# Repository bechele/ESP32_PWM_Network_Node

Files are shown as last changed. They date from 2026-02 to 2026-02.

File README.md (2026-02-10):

## Network device to drive Servos for Animatronics:

With the latest Software 3.0 the Bechele software (https://github.com/bechele/bechele) now supports beside the existing PCA9685 PWM Boards also network devices, based on cheap ESP32 modules. Each network device may handle 16 Servos or 16 Relais or a desired mixture of both. All the data transfers from the Host (Raspi) is realized using broadcast transmissions, where all devices (nodes) receive the same data packets. According to the node configuration, the node takes the data from the packet that is intended for it. This way there is plenty of time to drive 700 Servos @ 44 ESP32 nodes, or 11000 relais @ 700 nodes with a 50ms refresh rate. Network devices may be connected via Ethernet or WiFi. Of course Ethernet driven nodes are more stable than via Wifi. The board exists in two flavours. A smaller SMD version and a larger version unsing conventional parts. For both versions you may download the gerber files and also the kicad source, so you can order a PCB from your desired PCB manufacturer. The smd version is for skilled people who know how to handle and solder SMD parts. The conventional Version uses mainly larger parts that are much easier to solder onto the PCB. Which one you use is up to you. The function is identical.<br><br>
**Note: Using Wifi is by far not as safe as using ethernet. To use WiFi, you need to make sure, the WiFi router is very close to the network devices, since the RSSI (Received Signal Strength Indicator) must be below 70 dB, (you may read the RSSI value during boot, when connecting a serial monitor to the TX pin of the device). Otherwise you will notice lots of missing packets – means the movement of your servos will be not continuous. Also you need an environment where there are only few other Wifi radio sources. If there is a lot of other traffic around, you will encounter the same problems. This is due to the working principle of WiFi and has nothing to do with the software. Wifi is not intended for real time control of devices ! So my recommendation is to use W5500 Ethernet modules. In a test using Ethernet with 700 configured Servos @ 50 ms refresh rate (means every 50 ms all servos got new data), none of the packets went lost over a longer time, so ethernet is quite safe.**
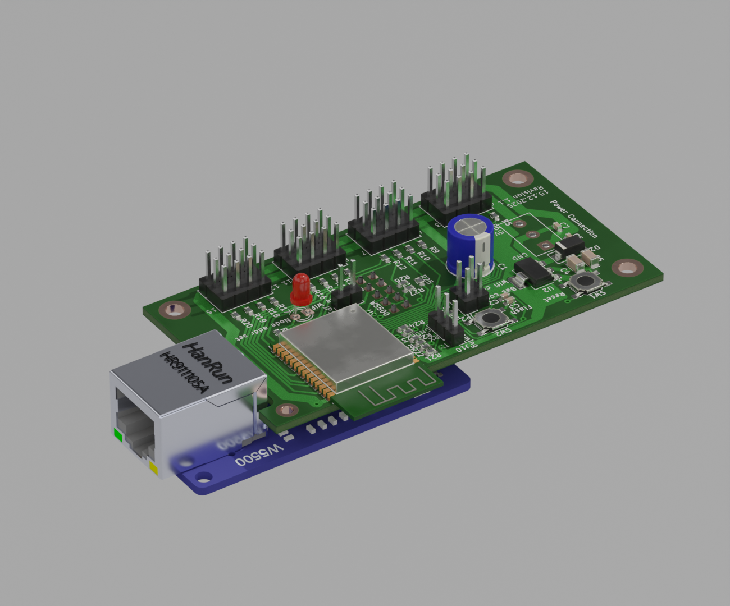
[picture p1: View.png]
ESP32 Node Image


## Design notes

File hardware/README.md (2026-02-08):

## The ESP32_PWM_NODE_PCB exists in two flavours:
- A SMD based version for skilled people, able to solder tiny SMD parts, or for automatic assembled PCBs.
- A PCB based on conventional parts for easier assembly.

Note: Both PCBs have an identical function and run with the same firmware.

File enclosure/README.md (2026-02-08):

## Enclosures - cases for the ESP32_PWM_NODE_PCBs
There exist four different cases for ESP32_PWM_NODE PCBs - depending on which PCB you use and if you want to use the W5500 Ethernet network module:
- An enclosure for the SMD based PCB with W5500 Ethernet module.
- An enclosure for the SMD based PCB, but omitting the W5500 Ethernet module.
- An enclosure for the conventional parts based PCB with W5500 Ethernet module.
- An enclosure for the conventional based PCB, but omitting the W5500 Ethernet module.

All enclosures are available as .stl file for 3d printing and as an .obj file for reworking.

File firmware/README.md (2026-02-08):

## This firmware is intended for the ESP32_PWM_NODE_PCB.
It manages to receive broadcast data packets from the bechele software https://github.com/bechele/bechele and controls servos and relais connected to the ESP32_PWM_NODE_PCB.
The firmware needs the enclosed Library that derives from:
https://github.com/ramadhanafif/Ethernet2-W5500-ESP32.
For details read the documentation in folder Documentation and/or visit my web site: http://bechele.de

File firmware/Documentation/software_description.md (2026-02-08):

# Software description for the Bechele Project network devices.
## Features of the Bechele Network devices:
* The bechele project can use new, extremely cheap hardware, based on a ESP32 Wroom 32 or ESP32E Wroom. Furhter called nodes.
* very large installations may be easily realized using the bechele software, since Hundrets of nodes may be controlled simultaneously by the bechele software.
* A node has 16 output channels - means 16 Servos may be connected directly to one small hardware box.
* A node may also be used to connect binary outputs, such as relais boards
* The 16 output pins can be split into partially Servo or relais outputs in a flexible way.
* Currently approx. 32000 nodes may be addressed in one network.
* A node may have a W5500 device attached, so it gets its data via 100BaseT Ethernet.
* All nodes have built in Wifi.
* The device can be fully configured over the network, once the basic configuration has been done. 
* The network traffic remains on an absolute minimum, since data is sent via broadcast to all nodes at once. 
* With the limited packet length of 1432 bytes per network frame, approx 700 nodes may be controlled by the bechele software simultaneously. If more is required, the software may be adapted easily.
The default 50 ms (20Hz) refresh time allows seamless servo movements without stucks or visible delays.

## Description of the internal software function
The Bechele project uses an ESP32 Wroom 32 or ESP32E Wroom as an output device in the Ethernet and WLAN network. The ESP can receive data transmitted via broadcast from the network on port 7625. The user datagram for normal operation has an indefinite length but always begins with a data word (16 bits) containing the number of transmitted user data words. The second data word contains a sequential counter, which is not initially important for the receiver. This is followed by further data words (16 bits) which, for servo data, are in the range of 0-4095 (0FFFh) and are output as PWM values to the ESP's available PWM outputs (max. 16), depending on the configuration. For relay data, the valid value range is between 0 and 65535. A single data word can control all 16 outputs of the ESP. The outputs provide sufficient drive current to control model servos or relay modules. Depending on the software configuration, each of the 16 outputs can be operated either as a servo output with PWM or as a digital output with a constant level. Mixed operation between servo and relay outputs is also possible. The specific word in the datagram used for output is defined in configuration registers. This can be any data word in the datagram; it does not need to be synchronized to the 16 available outputs (steps), but it must be synchronized to the data word boundary. This means that the start word is specified in the configuration register in word steps, not as a byte position in the datagram. There can be multiple of these modules in the network, referred to as nodes. The maximum number of nodes in the network is set to 32765. As a result, the most significant bit in the length field of the datagram is not used for output addressing. If the length word (the first word in the datagram) contains a value greater than 32767, then the payload in the datagram is interpreted as a configuration instruction. Each node has a jumper input port (Bas conf) that is set to enable a basic configuration for the node. Nodes without the jumper set will not respond to the length value of 32768, as they are not in basic configuration mode. In basic configuration mode (with the jumper set) the sender of the broadcast will send the Ethernet address in the first six payload data words, followed by the node address and a 16-bit checksum. The ESP remembers its addresses, provided the checksum is correct, and stores them in NV memory (as an address register). The basic configuration datagram has a length of seven payload data words plus the checksum, resulting in a total length of 20 bytes. Once the ESP has received its Ethernet and node addresses, it automatically reboots when the jumper is removed. After the reboot, the new MAC and node addresses are applied. If a valid address exists in NV memory, a permanently assigned output port is set to 1. An LED connected to the node signals to the user that the address and MAC address for that node have been set. The address range for node addresses extends from 32769 (node 1) to the word boundary of 65533 (node 32765). If the first datagram word contains the node's address (+32768), the datagram's payload is considered the configuration for that node. Incoming configuration data is stored in 16-bit configuration data registers located in the NV data area or in the ESP's RAM. Multiple registers can be addressed simultaneously in a configuration datagram. Starting with data word 2 (word 0 encodes the node address, and word 1 is the sequential counter), each subsequent word is considered the register address, and the following word is the register content. The number of registers in a configuration datagram is undefined. As long as the datagram does not end, any two consecutive data words are treated as a single register instruction. Both configuration data and user data are broadcast to port 7625. For later physical node identification in a configured network, the configuration program nodeconfig.pl can send a blink command (register 128) to the node address to be identified, whereupon the node's LED blinks at a rate of 0.5 seconds. All configuration commands and PWM user data use a 16-bit checksum.

## The following registers in the NV memory are occupied:
```
Registers 0-5: Ethernet address of the node. 
6: Node address. 
7: Number of PWM outputs. 
8: Start word in the payload datagram (equal to the servo number in the operating program) containing the payload data applicable to this node. 
9: Pin number to which the PWM start word is output. All subsequent PWM data words are output to the following pins until the number (7:) is reached. 
10: Number of output pins reserved for relays. 
11: Data word in the payload datagram (servo number) containing the bit data for the output pins, where 16 bits represent 16 outputs. 
12: Pin number to which the first bit in the payload data word is mapped.
```
## The following registers in RAM are active: 
```
Register 128: Blinking active
Register 129: Blinking duration in seconds - currently unused by the configuration software. 
Register 130: Node reset - as soon as this register is set to 1, the ESP performs a reboot. 
Register 131: Status report to host via UDP (unicast) on port 7626. 
Register 132: Unconfig Node - if this register is set to 1, all registers are set to the default value 0 and a reboot is performed. This means the box will then be in its factory default state and must undergo a basic and node configuration before use.
```
## Two additional commands exist that are executed by all nodes on the network.

1. 65535 in the datagram's length word: Deactivates all PWM outputs. This is usually issued after a session ends to protect the servos.
2. 65534 in the datagram's length word: Restarts all nodes.

# Hardware:
A W5500 network adapter may be connected. If it is detected, it is initialized and Wi-Fi is disabled. If initialization fails, the node will still wait for a network connection via Ethernet - meaning there is no fallback to Wi-Fi.
If the node should use Wi-Fi, the "force Wi-Fi" jumper can be removed - this step requires a reboot.
The ESP obtains its IP network address via DHCP. In Ethernet mode, the ESP does not respond to unicast packets. The only communication with the ESP occurs via broadcasts on port 7625. Therefore, a network ping provides no information about the node's functionality.
The initial Ethernet address is set to DE:AD:BE:EF:00:01 in basic configuration mode (Bas Conf Jumper). This means that each module must be initialized separately, one after the other; otherwise, the same Ethernet address will be assigned to two or more nodes during basic configuration.

# Configuration procedure for Ethernet and Wi-Fi (after basic Wi-Fi configuration):
```
1. Set the Basic Config jumper.
2. Reset the node using the reset button on the board.
3. Set the node address in the configuration program nodeconfig.pl - the Ethernet address will be assigned automatically.
4. Press the Basic Config button in the configuration program.
5. Remove the Basic Config jumper from the node. This will automatically reboot the node. After a few seconds, the LED on the node should light up. This indicates that the basic configuration was successful.
6. Select the node address that was just set - if it is not already active - and use the "Get_Node_Status" button to display the node's configuration. If OK, you can proceed to step 7.
7. Set the remaining configuration parameters, which are usually different for each node.
8. Press the "Send_Node_Setup" button - the remaining parameters will be set. If the associated automatic check is successful, the configuration for this node is marked as "confirmed" in the database used by nodeconfig.pl.
9. The node is then ready to receive and output PWM and binary data. No further configuration is required after switching the node off and on again.
```
## Configuration procedure for Wi-Fi:
```
Note: The jumper "0= force wifi" must not be set:
1. Activate the Wi-Fi manager via the "Wifi Conf" jumper.
2. Reset the node using the reset button on the board.
3. Select the access point "ESP32_PWM_Node" on the host (smartphone or computer).
4. The Wi-Fi manager will start automatically, depending on the device.
5. Configure the Wi-Fi network (SSID and Wi-Fi password).
6. Save and remove the "Wifi Conf" jumper.
7. Now proceed with the basic configuration as described in the configuration procedure.
```

# Summary in brief:

## Datagram description Basic configuration when length word = 32768:
```
1st word (0) in the datagram = Length word
2nd word (1) in the datagram = Sequential number
3rd word (2) in the datagram = MAC 1 - Register -> 0
4th word (3) MAC 2 - Register -> 1
5th word (4) MAC 3 - Register -> 2
6th word (5) MAC 4 - Register -> 3
7th word (6) MAC 5 - Register -> 4
8th word (7) MAC 6 - Register -> 5
9th word (8) Node address -> 6
10th word (9) CRC checksum
Total length of a basic configuration command = 20 bytes
```

## Datagram description for Configuration mode when length word > 32768:
```
1. Word (0) in the datagram = Length word (over 32768 (8000H 32769 to 65533))
2. Word (1) in the datagram = Sequential number
3. Word (2) Register number to be set
4. Word (3) Register content
5. Word (4) Register number to be set (Optional if multiple registers are to be set)
6. Word (5) Register content (Optional)
..
..
Last word = CRC checksum
```
Calculation of the node address from the length word: 
Node address = Length word - 32768 (received on ESP side), Node address = Node + 32768 (send from host side) Range 1-32765 (32765 nodes maximum)

## Datagram description in payload mode: if length word < 32768:
1st word (0) in the datagram = Length word less than 32768 (8000H)
2nd word (1) in the datagram = Sequential number
3rd word (2) up to -> 32767 = Normal PWM and relay data
..
..
Last word = CRC checksum

## Registers 0-127 are NV (permanent) Register:
```0-5: MAC address
6: Node address
7: Number of active PWM pins (0-16)
8: Servo number assigned to the first configured pin. All subsequent servo data is assigned to the following pins until the number of pins is exhausted.
9: Pin number to which the servo number in 8 is mapped
10: Number of active relay pins (0-16)
11: Servo number containing the relay bit data
12: Pin number to which the first relay bit is mapped. (A word contains 16 bits - each bit can define a digital output, bits 0-15). If the pin number is not zero, the bit data is shifted accordingly.
```
## Registers 128 to 255 are RAM registers:
```128 Blinking active
129 Blink duration - currently not used by the configuration program
130 If set, a targeted reboot of the node is performed
131 Status report to host via unicast UDP (0x0001 as configuration date) to the server host. This register is cleared (00) after a single execution, meaning the host must poll for status updates.
132 Reset node to default values - this means it must be completely    reconfigured. Only the Wi-Fi configuration remains.
```
## Jumper functions:
```Jumper Bas Conf: -> sets MAC address and node address
Jumper WIFI Conf: -> starts the Wi-Fi Manager web interface to set the SSID and password
Jumper 0=force Wi-Fi: -> if removed, or if no W5500 board is present, Wi-Fi is used
```
# FYI:
A problem arises with mixed PWM and binary outputs: While the output start positions can be freely defined, the number of outputs must match the pin boundaries. If the pin boundaries are misconfigured, the configuration program nodeconfig.pl will issue warning messages. However, the program cannot verify which data will be servo or relay data, nor can it check if these are correctly assigned, because the data in the datagram is the same for both relays and servos. (1 word per PWM value, and 1 word = 16 bits = max. 16 relay pins). This means the user must ensure the correct start words are configured. Otherwise, PWM values may be interpreted as binary values for digital port outputs, or vice versa. Example: Number of PWM outputs: 12 (12 words); Number of binary outputs: 4 (1 word); PWM start position: 20 - ranges to 31. If binary outputs are located in between - for example, relay start 24 - then the binary and PWM values will overlap. This means the binary data is output as PWM to the 5th servo. The binary outputs would be correctly displayed in this case. We have to accept this. The advantage of the flexible start position determination, and thus the distribution between servo and relay outputs, lies in the fact that some nodes only have to control a few servos, while others control the entire number. This means the host software doesn't have to strictly adhere to node boundaries; instead, logically related servo and relay ranges can be created sequentially. Which node controls which function is determined during node configuration. Incidentally, the start positions (servos/relays) in the datagram for a node don't have to be adjacent. If desired, all servos for all nodes can be placed at the beginning of the datagram and all relays at the end, or vice versa. What doesn't work is having two or more servo or relay ranges per node, because only one configuration set exists per node.

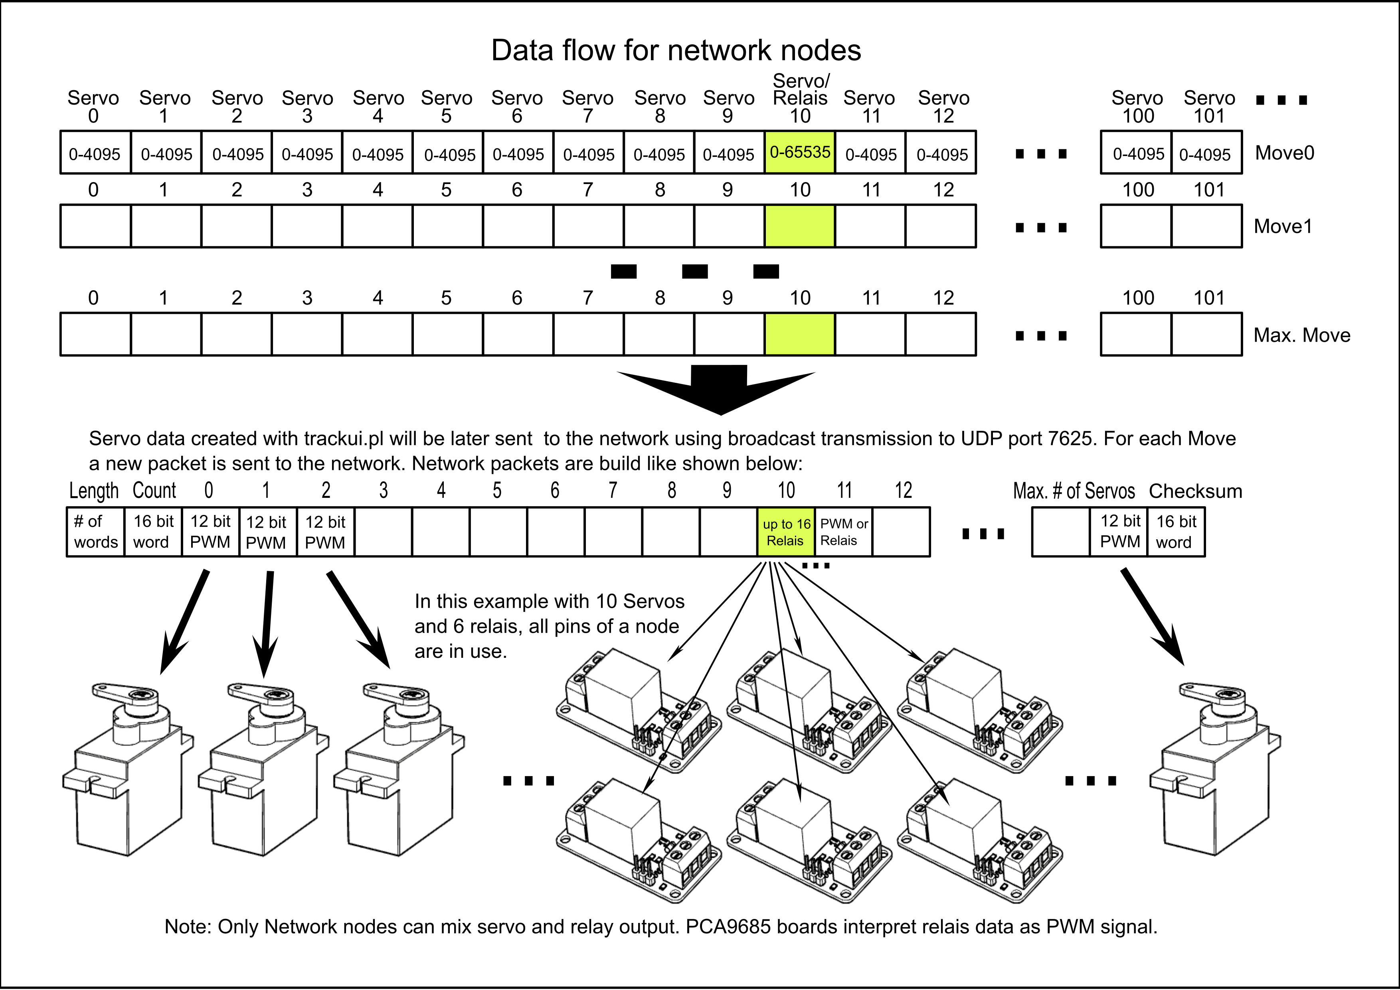
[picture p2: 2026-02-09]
firmware/Documentation/dataflowchart.png

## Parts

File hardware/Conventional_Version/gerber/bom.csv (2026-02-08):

Designator | Footprint | Quantity | Value | LCSC Part #
C1 | CP_Radial_D8.0mm_P3.50mm | 1 | 470µ
C2, C3 | C_Axial_L5.1mm_D3.1mm_P7.50mm_Horizontal | 2 | 1nF
C4 | CP_Radial_D5.0mm_P2.50mm | 1 | 10µf
C5 | CP_Radial_D5.0mm_P2.50mm | 1 | 22µf
C6, C7 | C_Disc_D6.0mm_W2.5mm_P5.00mm | 2 | 100nF
D1 | LED_D3.0mm | 1 | Node addr set
D2 | D_DO-41_SOD81_P7.62mm_Horizontal | 1 | SS14
J1 | W5500_Modul | 1 | W5500
J10 | PinHeader_1x03_P2.54mm_Vertical | 1 | Programming
J11 | TE_826576-3_1x03_P3.96mm_Vertical | 1 | Power Connection
J2, J3, J4, J5 | PinHeader_2x04_P2.54mm_Vertical | 4 | ~
J6, J7, J8, J9 | PinHeader_1x04_P2.54mm_Vertical | 4 | ~
JP1 | PinHeader_1x02_P2.54mm_Vertical | 1 | 0 = force WIFI
JP2 | PinHeader_1x02_P2.54mm_Vertical | 1 | Bas conf
JP3 | PinHeader_1x02_P2.54mm_Vertical | 1 | Wifi conf
R1, R2, R23, R25, R26, R27, R4 | R_Axial_DIN0207_L6.3mm_D2.5mm_P2.54mm_Vertical | 7 | 10K
R10, R11, R12, R13, R14, R15, R16, R17, R18, R19, R20, R5, R6, R7, R8, R9 | R_Axial_DIN0207_L6.3mm_D2.5mm_P2.54mm_Vertical | 16 | 120
R21 | R_Axial_DIN0207_L6.3mm_D2.5mm_P10.16mm_Horizontal | 1 | 470
R22 | R_Axial_DIN0207_L6.3mm_D2.5mm_P10.16mm_Horizontal | 1 | 10K
R24 | R_Axial_DIN0207_L6.3mm_D2.5mm_P2.54mm_Vertical | 1 | 470
R3 | R_Axial_DIN0207_L6.3mm_D2.5mm_P2.54mm_Vertical | 1 | 220
SW1 | SW_PUSH_6mm | 1 | Reset
SW2 | SW_PUSH_6mm | 1 | Flash
U1 | ESP32-WROOM-32 | 1 | ESP32-WROOM-32
U2 | SOT-223-3_TabPin2 | 1 | AMS1117-3.3

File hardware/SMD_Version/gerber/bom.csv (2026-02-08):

Designator | Footprint | Quantity | Value | LCSC Part #
C1 | CP_Radial_D8.0mm_P3.50mm | 1 | 470µ
C2, C3 | 0603 | 2 | 1nF
C4 | 1206 | 1 | 10µf
C5 | 1206 | 1 | 22µf
C6, C7 | 0603 | 2 | 100nF
D1 | LED_D3.0mm | 1 | Node addr set
D2 | D_SMA | 1 | SS14
J1 | W5500_Modul | 1 | W5500
J10 | PinHeader_1x03_P2.54mm_Vertical | 1 | Programming
J11 | TE_826576-3_1x03_P3.96mm_Vertical | 1 | Power Connection
J2, J3, J4, J5 | PinHeader_2x04_P2.54mm_Vertical | 4 | ~
J6, J7, J8, J9 | PinHeader_1x04_P2.54mm_Vertical | 4 | ~
JP1 | PinHeader_1x02_P2.54mm_Vertical | 1 | 0 = force WIFI
JP2 | PinHeader_1x02_P2.54mm_Vertical | 1 | Bas conf
JP3 | PinHeader_1x02_P2.54mm_Vertical | 1 | Wifi conf
R1, R2, R22, R23, R25, R26, R27, R4 | 0603 | 8 | 10K
R10, R11, R12, R13, R14, R15, R16, R17, R18, R19, R20, R5, R6, R7, R8, R9 | 0603 | 16 | 120
R21, R24 | 0603 | 2 | 470
R3 | 0603 | 1 | 220
SW1 | SW_SPST_SKQG_WithoutStem | 1 | Reset
SW2 | SW_SPST_SKQG_WithoutStem | 1 | Flash
U1 | ESP32-WROOM-32 | 1 | ESP32-WROOM-32
U2 | SOT-223-3_TabPin2 | 1 | AMS1117-3.3

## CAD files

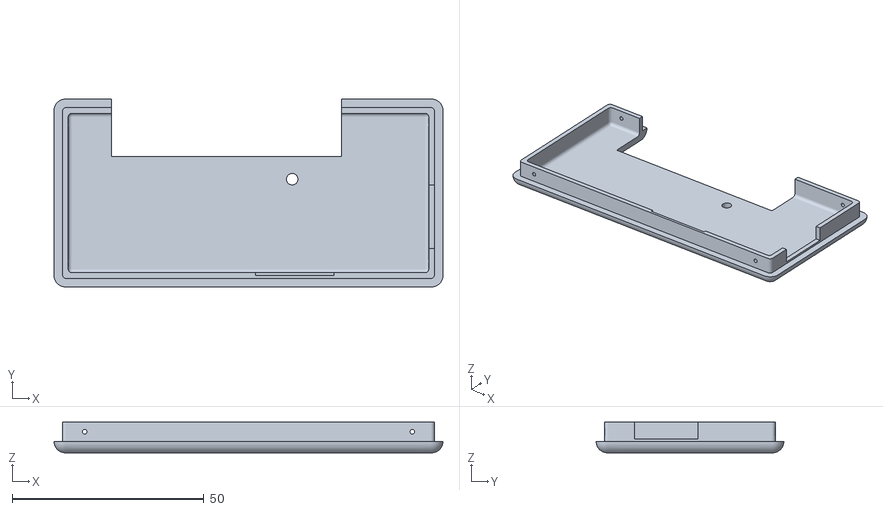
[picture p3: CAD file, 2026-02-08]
enclosure/STL/Case_Top_W5500_PWM_Device_SMD.stl
101.5 x 49.0 x 8.00

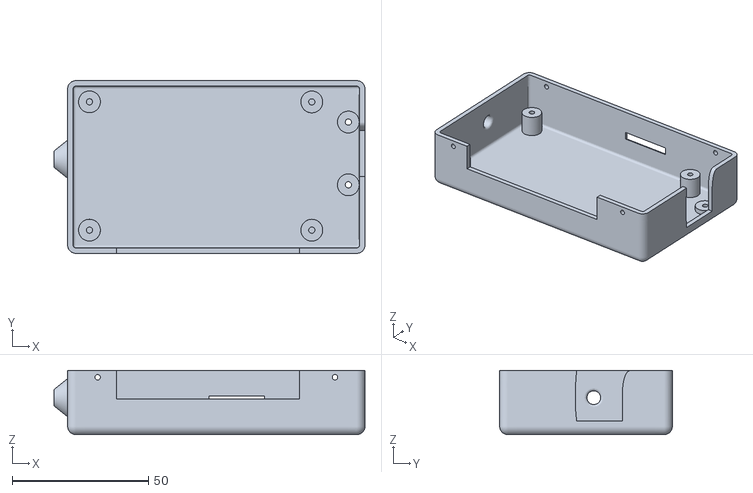
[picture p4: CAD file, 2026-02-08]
enclosure/STL/Case_Bottom_W5500_PWM_Device_Conventional.stl
114.0 x 63.3 x 23.5

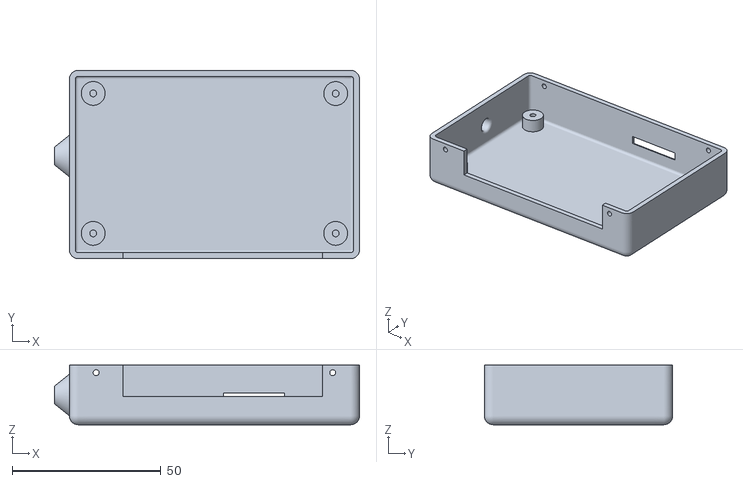
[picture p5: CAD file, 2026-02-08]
enclosure/STL/Case_Bottom_WiFi_PWM_Device_Conventional.stl
102.5 x 63.3 x 20.0

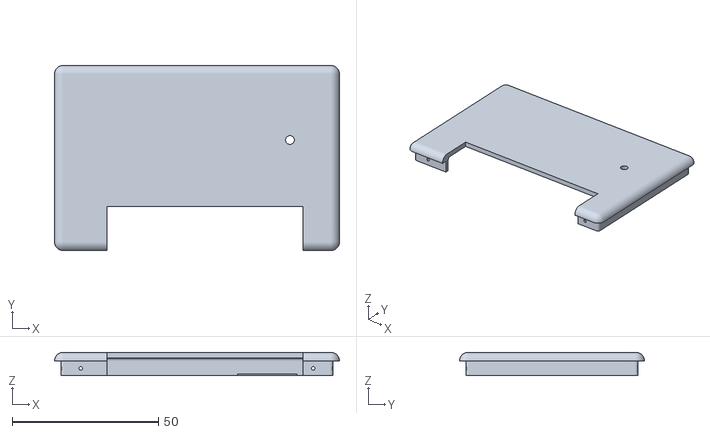
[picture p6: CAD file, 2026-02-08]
enclosure/STL/Case_Top_WiFi_PWM_Device_Conventional.stl
97.5 x 63.3 x 8.00

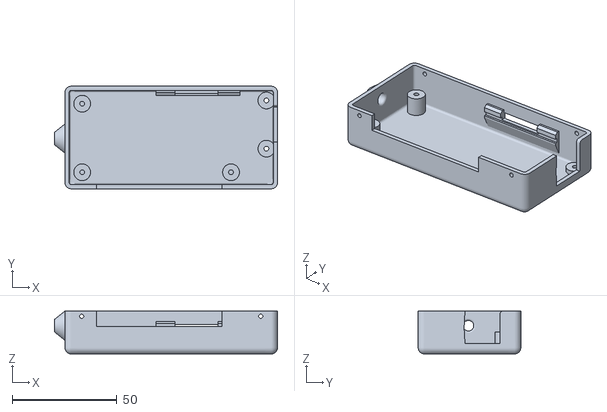
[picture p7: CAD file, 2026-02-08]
enclosure/STL/Case_Bottom_W5500_PWM_Device_SMD.stl
106.5 x 49.0 x 20.5

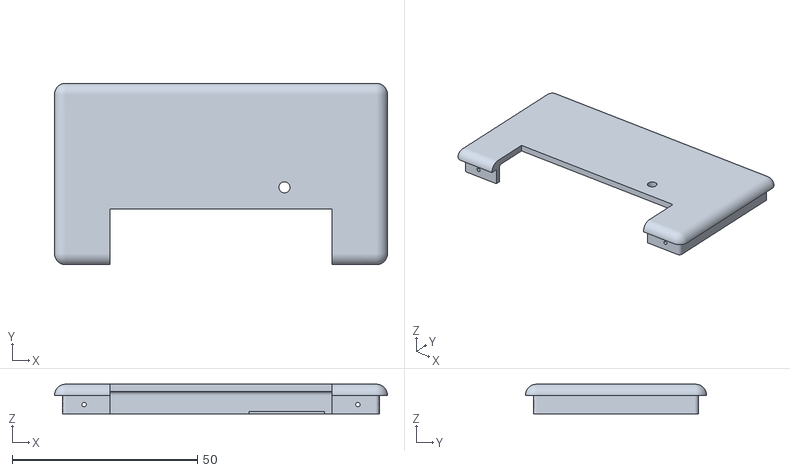
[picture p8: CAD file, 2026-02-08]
enclosure/STL/Case_Top_WiFi_PWM_Device_SMD.stl
90.0 x 49.0 x 8.00

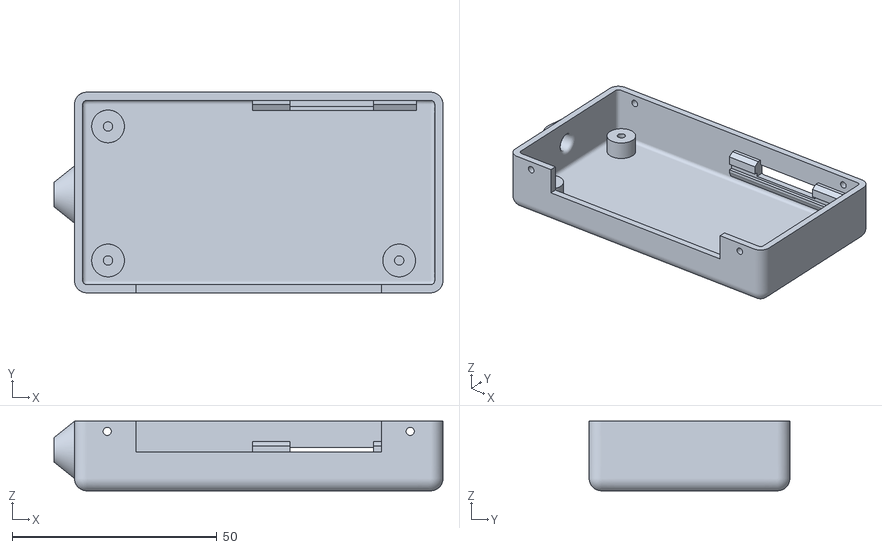
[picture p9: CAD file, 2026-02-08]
enclosure/STL/Case_Bottom_WiFi_PWM_Device_SMD.stl
95.0 x 49.0 x 17.0

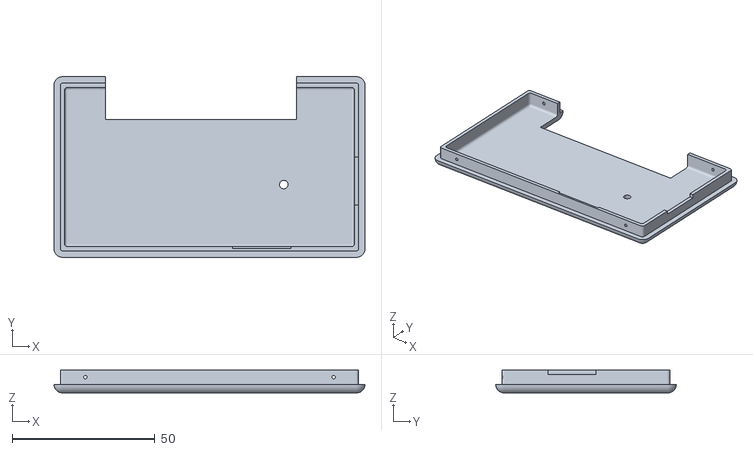
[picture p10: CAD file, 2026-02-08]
enclosure/STL/Case_Top_W5500_PWM_Device_Conventional.stl
109.0 x 63.3 x 8.00

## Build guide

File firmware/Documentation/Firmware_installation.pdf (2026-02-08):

07.Feb.2026

## Installation instructions for the ESP32PWMPCB_Firmware 1.1:

1: Installation via Arduino IDE - from source
⦁ You need to have the Arduino IDE installed onto your computer
⦁ Install ESP32 Support via the board manager: Arduino ESP32 Boards and esp32 by Espressif
⦁ Install the following Libraries: WiFi Manager by tapzu,Ethernet2 fom the enclosed Library - !!!! NOT THE ONE FROM THE LIBRARY MANAGER !!!!
⦁ You need to install the enclosed file "Ethernet2-W5500-ESP32.zip" to your library folder of your IDE -> Sketch -> Include Library -> Add .ZIP Library -> select enclosed library
⦁ open your .ino file into your arduino ide
⦁ Connect a serial 3.3V level interface to your ESP Board to pin RX, TX and GND
⦁ select the Board In the IDE: Tools->Board: esp32 -> ESP32 Dev Module
⦁ select the Com port of your serial interface: COM "X" usually not COM 1
⦁ select your ESPs operation data, under tools like CPU Frequency, upload speed etc. Keep the default, if you do not know.
⦁ Press the Peset and Flash button simultaneously on you ESP PCB.
⦁ Release first the reset button and after that the flash button - now the ESP is in flash mode and waits for uploads.
⦁ Press the upload button in the IDE and wait until it compiled - ignore warnings. The upload should start automatically.
⦁ After that your ESP node is ready for setup via nodeconfig.pl from the bechele software.

2: Installation via Flash download tools from Espressif from the enclosed pre-compiled .bin file.
⦁ Download the tool from https://www.espressif.com/en/support/download/other-tools -https://dl.espressif.com/public/flash_download_tool.zip
⦁ Install the tool
⦁ Run the tool:

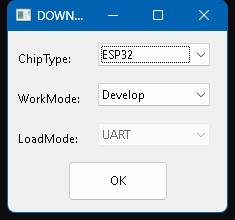
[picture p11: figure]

⦁ Select ESP32 and Develop -> OK
⦁ Connect a serial 3.3V level interface to your ESP Board to pin RX, TX and GND
⦁ Select the file to upload and enter address 0x0000: Also set com port and upload speed. Then press "START"

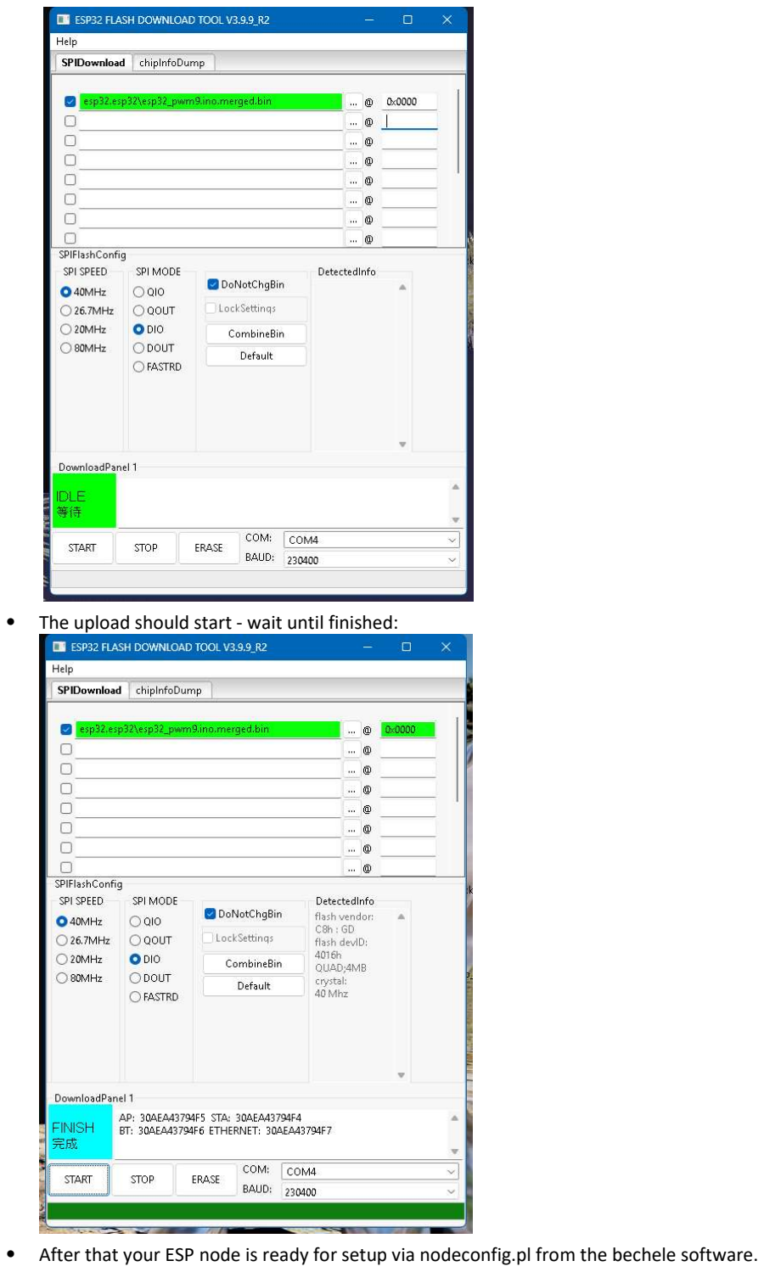
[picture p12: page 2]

⦁ The upload should start - wait until finished:

⦁ After that your ESP node is ready for setup via nodeconfig.pl from the bechele software.

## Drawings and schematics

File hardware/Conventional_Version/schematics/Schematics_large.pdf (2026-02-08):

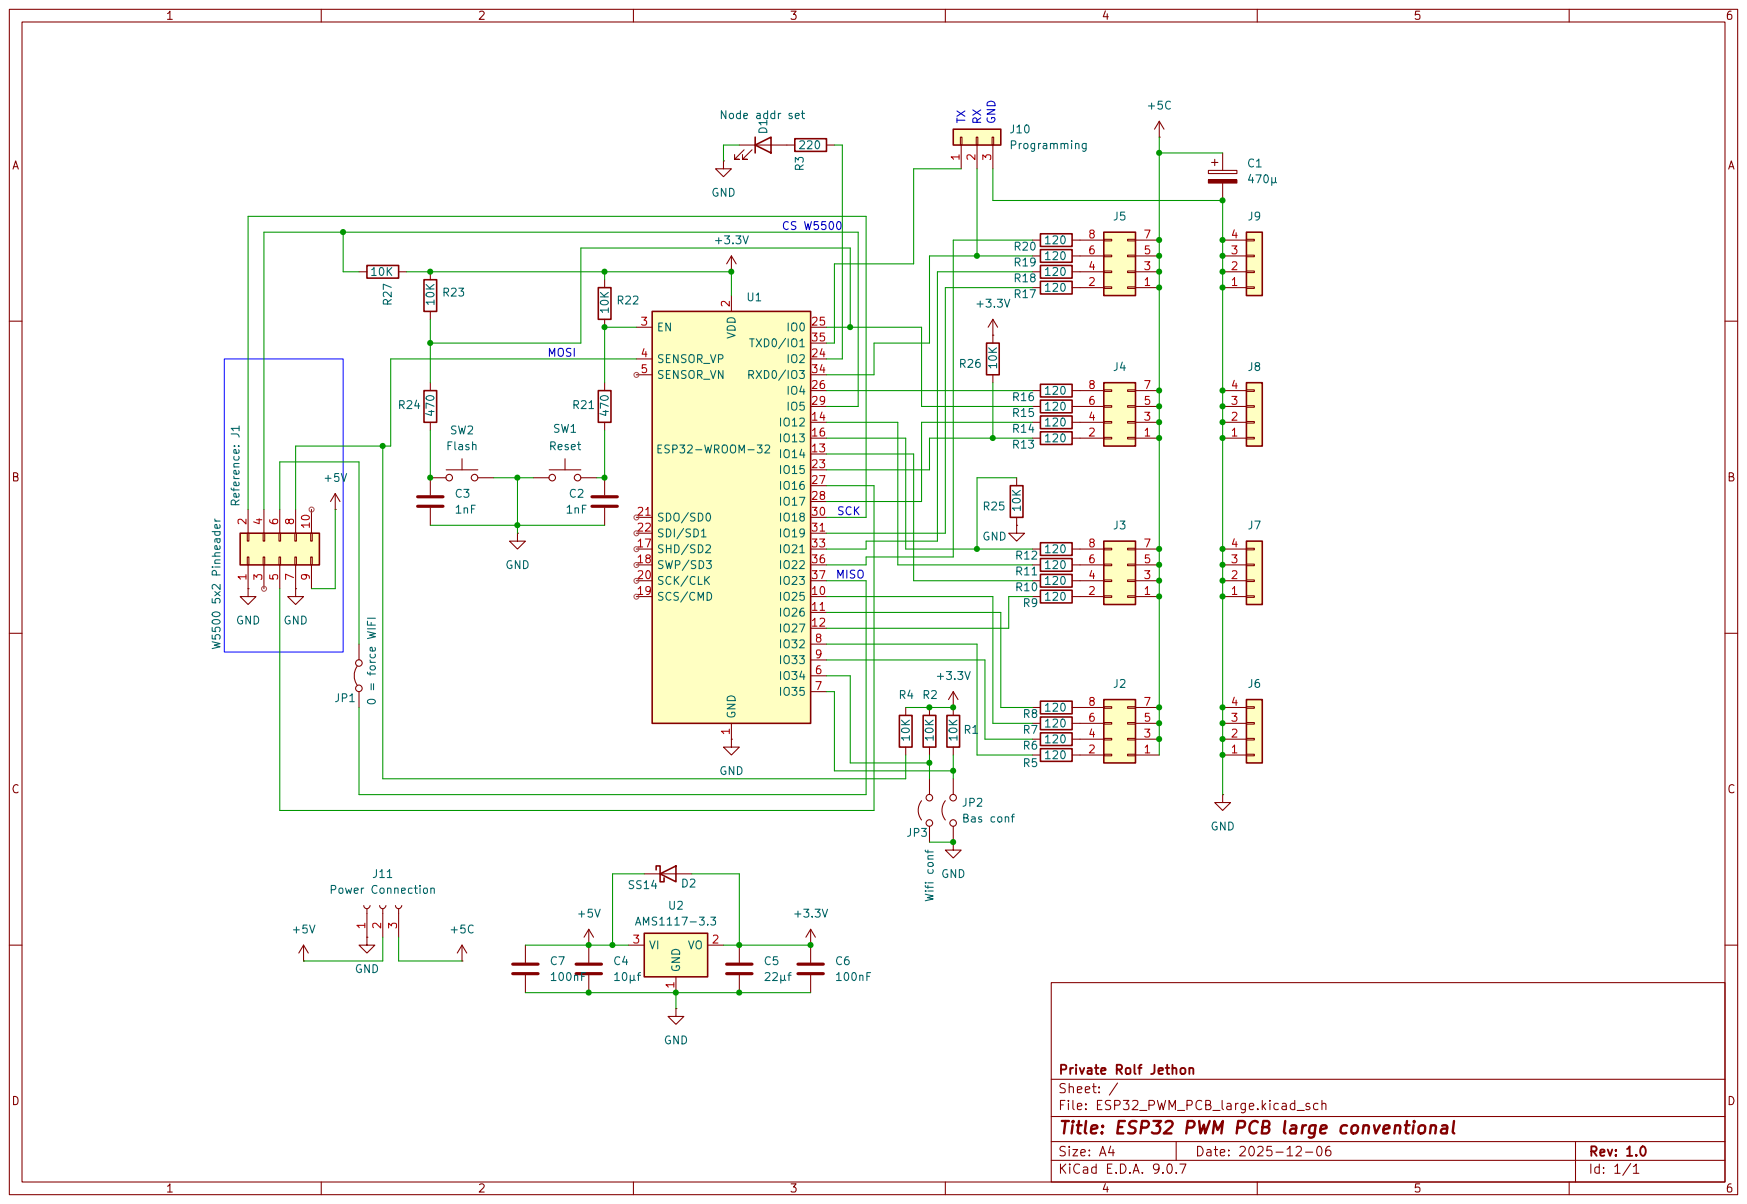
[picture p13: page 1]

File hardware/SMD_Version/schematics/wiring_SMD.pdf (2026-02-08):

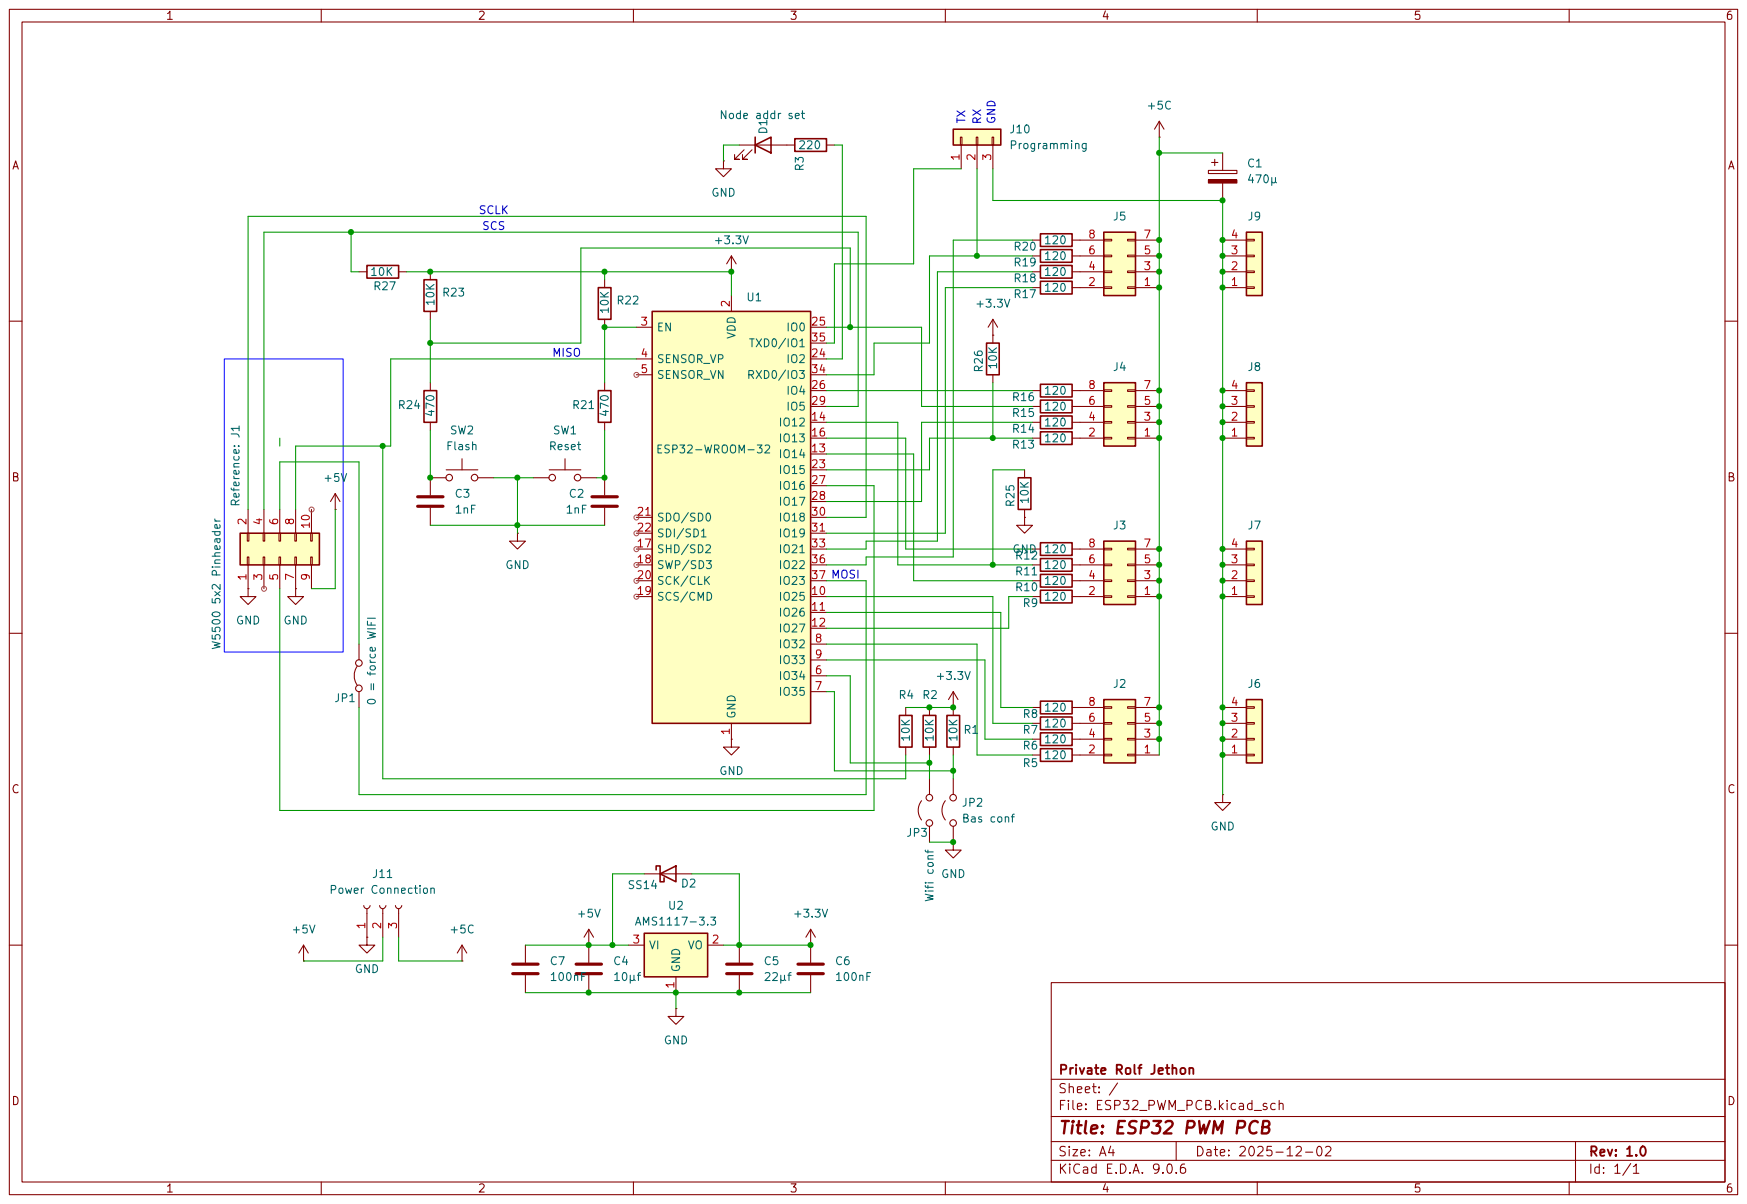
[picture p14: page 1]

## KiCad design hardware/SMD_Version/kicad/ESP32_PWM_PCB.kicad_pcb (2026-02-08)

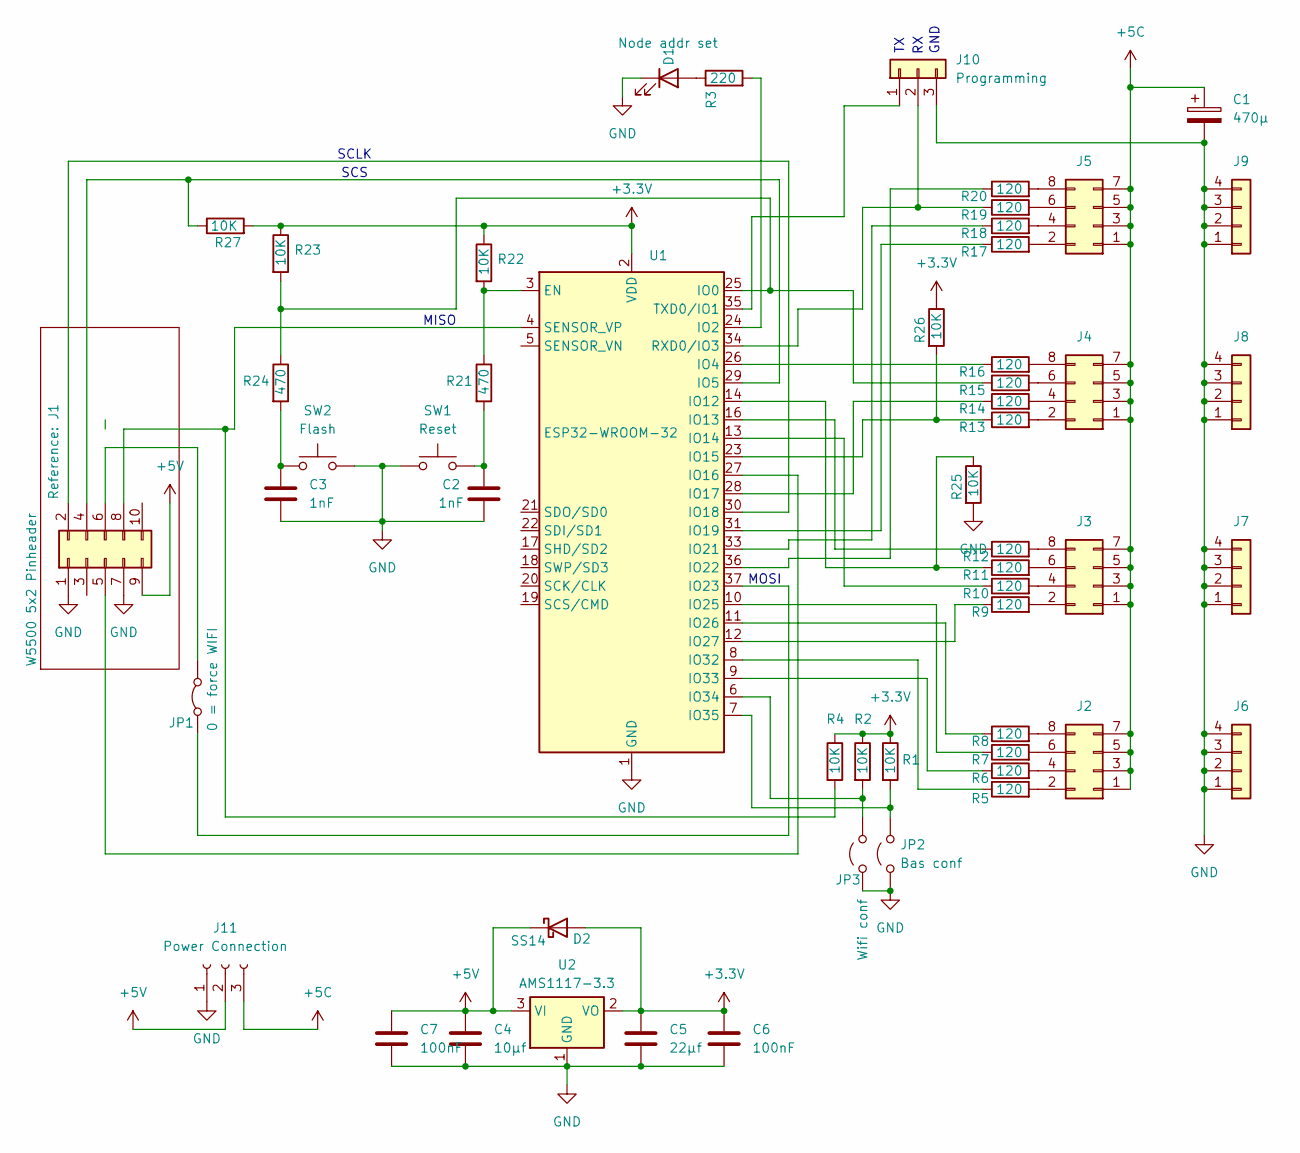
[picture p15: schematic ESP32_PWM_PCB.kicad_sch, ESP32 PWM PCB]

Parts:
C1: 470µ; CP_Radial_D8.0mm_P3.50mm
C2, C3: 1nF; C_0603_1608Metric
C4: 10µf; C_1206_3216Metric
C5: 22µf; C_1206_3216Metric
C6, C7: 100nF; C_0603_1608Metric
D1: Node addr set; LED_D3.0mm
D2: SS14; D_SMA
J1: W5500 5x2 Pinheader; W5500_Modul
J2, J3, J4, J5: PinHeader_2x04_P2.54mm_Vertical
J6, J7, J8, J9: PinHeader_1x04_P2.54mm_Vertical
J10: Programming; PinHeader_1x03_P2.54mm_Vertical
J11: Power Connection; TE_826576-3_1x03_P3.96mm_Vertical
JP1: 0 = force WIFI; PinHeader_1x02_P2.54mm_Vertical
JP2: Bas conf; PinHeader_1x02_P2.54mm_Vertical
JP3: Wifi conf; PinHeader_1x02_P2.54mm_Vertical
R1, R2, R4, R22, R23, R25, R26, R27: 10K; R_0603_1608Metric
R3: 220; R_0603_1608Metric
R5, R6, R7, R8, R9, R10, R11, R12, R13, R14, R15, R16, R17, R18, R19, R20: 120; R_0603_1608Metric
R21, R24: 470; R_0603_1608Metric
SW1: Reset; SW_SPST_SKQG_WithoutStem
SW2: Flash; SW_SPST_SKQG_WithoutStem
U1: ESP32-WROOM-32
U2: AMS1117-3.3; SOT-223-3_TabPin2

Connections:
+3.3V: C5.1, C6.1, D2.2 (A), R1.1, R2.1, R4.1, R22.1, R23.1, R26.1, R27.2, U1.2 (VDD), U2.2 (VO)
+5C: C1.1, J2.1, J2.3, J2.5, J2.7, J3.1, J3.3, J3.5, J3.7, J4.1, J4.3, J4.5, J4.7, J5.1, J5.3, J5.5, J5.7, J11.3
+5V: C4.1, C7.1, D2.1 (K), J1.9 (5V), J11.2, U2.3 (VI)
GND: C1.2, C2.2, C3.2, C4.2, C5.2, C6.2, C7.2, D1.1 (K), J1.1 (GND), J1.7 (GND), J6.1, J6.2, J6.3, J6.4, J7.1, J7.2, J7.3, J7.4, J8.1, J8.2, J8.3, J8.4, J9.1, J9.2, J9.3, J9.4, J10.3, J11.1, JP2.1 (A), JP3.1 (A), R25.2, SW1.1, SW2.2, U1.1 (GND), U1.15 (GND), U1.38 (GND), U1.39 (GND), U2.1 (GND)
unnamed: C2.1, R21.2, SW1.2
unnamed: C3.1, R24.2, SW2.1
unnamed: D1.2 (A), R3.1
unnamed: J1.8 (MISO), R4.2, U1.4 (SENSOR_VP)
unnamed: J1.6 (MOSI), JP1.2 (B)
unnamed: J1.5 (RST), U1.27 (IO16)
unnamed: J1.2 (SCLK), U1.30 (IO18)
unnamed: J1.4 (SCS), R27.1, U1.29 (IO5)
unnamed: J2.2, R5.2
unnamed: J2.4, R6.2
unnamed: J2.6, R7.2
unnamed: J2.8, R8.2
unnamed: J3.2, R9.2
unnamed: J3.4, R10.2
unnamed: J3.6, R11.2
unnamed: J3.8, R12.2
unnamed: J4.2, R13.2
unnamed: J4.4, R14.2
unnamed: J4.6, R15.2
unnamed: J4.8, R16.2
unnamed: J5.2, R17.2
unnamed: J5.4, R18.2
unnamed: J5.6, R19.2
unnamed: J5.8, R20.2
unnamed: J10.1, U1.35 (TXD0/IO1)
unnamed: J10.2, R19.1, U1.34 (RXD0/IO3)
unnamed: JP1.1 (A), U1.37 (IO23)
unnamed: JP2.2 (B), R1.2, U1.7 (IO35)
unnamed: JP3.2 (B), R2.2, U1.6 (IO34)
unnamed: R21.1, R22.2, U1.3 (EN)
unnamed: R15.1, R23.2, R24.1, U1.25 (IO0)
unnamed: R3.2, U1.24 (IO2)
unnamed: R16.1, U1.26 (IO4)
unnamed: R11.1, R25.1, U1.14 (IO12)
unnamed: R12.1, U1.16 (IO13)
unnamed: R10.1, U1.13 (IO14)
unnamed: R13.1, R26.2, U1.23 (IO15)
unnamed: R14.1, U1.28 (IO17)
unnamed: R17.1, U1.31 (IO19)
unnamed: R18.1, U1.33 (IO21)
unnamed: R20.1, U1.36 (IO22)
unnamed: R7.1, U1.10 (IO25)
unnamed: R8.1, U1.11 (IO26)
unnamed: R9.1, U1.12 (IO27)
unnamed: R5.1, U1.8 (IO32)
unnamed: R6.1, U1.9 (IO33)

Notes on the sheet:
GND
MOSI
SCLK
SCS
MISO

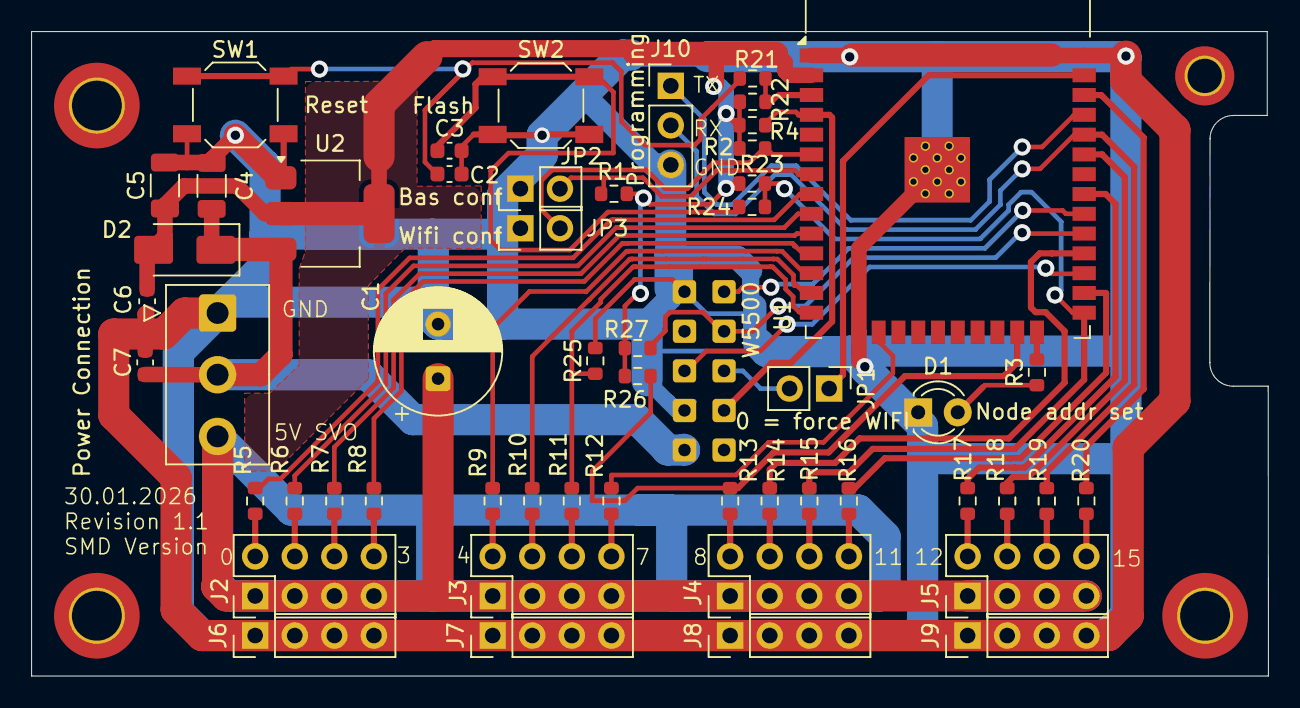
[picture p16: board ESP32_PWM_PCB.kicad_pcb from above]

Board: 2 copper layers, 79.4 x 41.4 mm, 54 parts (0 on the bottom side), 50 nets.

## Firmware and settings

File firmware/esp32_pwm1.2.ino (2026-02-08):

/* Firmware to read broadcasts on port 7625 from the network and output the 
   data as servo or relais movements. Intended to be used with 
   bechele software. https://bechele.de
   Copyright (C) <2026>  <Rolf Jethon>
   Version 1.2
   
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
   You should have received a copy of the GNU General Public License
   along with this program.  If not, see <http://www.gnu.org/licenses/>.*/

#include <WiFi.h>
#include <WiFiUdp.h>
#include <EEPROM.h>
#include <SPI.h>
#include <Ethernet2.h> 
#include <stddef.h> // for offsetof
#include "utility/w5500.h"

#include <WiFiManager.h>
extern SPIClass SPIe;
extern SPISettings wiznet_SPI_settings;

//--------------- W5500 SPI Pins -----------------------------------
#define W5500_SCK   18
#define W5500_MISO  36                                             // Not default, but necessary to have 16 PWM output pins
#define W5500_MOSI  23
#define W5500_CS    5
#define W5500_RST   16

byte mac[6] = {0xDE, 0xAD, 0xBE, 0xEF, 0x00, 0x01};                // Standard MAC

//------------- Network-configuration ------------------------------
#define FIRMWARE "Version 1.2"
#define UDP_PORT 7625
#define BROADCAST_IP "255.255.255.255"

//------------- EEPROM-Configuration -------------------------------
#define EEPROM_SIZE 512
#define NV_CONFIG_START 0

//---------- Configuration register Addresses ----------------------
#define REG_ETH_ADDR_1 1
#define REG_ETH_ADDR_2 2  nvConfig.nodeAddr = 0;

#define REG_ETH_ADDR_3 3
#define REG_ETH_ADDR_4 4
#define REG_ETH_ADDR_5 5
#define REG_ETH_ADDR_6 6
#define REG_NODE_ADDR 7
#define REG_PWM_COUNT 8
#define REG_BIN_OUT_COUNT 9
#define REG_PWM_START_WORD 10
#define REG_BIN_OUT_START_WORD_L 11
#define REG_BIN_OUT_START_WORD_H 12

//------------- W5500 Socket 0 Registers with BSB0=1 1-4=0 ---------
#define S0_MR       0x0000      // Socket 0 Mode Register
#define S0_CR       0x0001      // Socket 0 Command Register
#define S0_IR       0x0002      // Socket 0 Interrupt Register
#define S0_SR       0x0003      // Socket 0 Status Register
#define S0_PORT     0x0004      // Socket 0 Source Port (2 bytes)
#define S0_RX_RSR   0x0026      // Socket 0 Received Size Register (2 bytes)
#define S0_TX_WR    0x0024      // Socket 0 TX Write Pointer (2 Bytes)
#define S0_RX_RD    0x0028      // Socket 0 Read Pointer (2 bytes)

//------------- W5500 Common Registers with BSB0-4 =0 --------------
// #define MR       0x0000      // Mode Register - already defined in library
#define GAR         0x0001      // Gateway Address (4 bytes)
#define SUBR        0x0005      // Subnet Mask (4 bytes)
#define SHAR        0x0009      // Source Hardware Address (6 bytes) - MAC
#define SIPR        0x000F      // Source IP Address (4 bytes)
#define IR          0x0015      // Interrupt Register
#define IMR         0x0016      // Interrupt Mask Register
#define RTR         0x0017      // Retry Time Register (2 bytes)
#define RCR         0x0019      // Retry Count Register

//-------------- W5500 Control bytes -------------------------------
#define CB_WRITE_CR     0x0004  // Control Byte write common register
#define CB_WRITE_SR0    0x000C  // Control Byte write SR0 Register
#define CB_WRITE_TX0    0x0014  // Control Byte write TX buffer
#define CB_READ_CR      0x0000  // Control Byte Read common register
#define CB_READ_SR0     0x0008  // Control byte read SR0 register
#define CB_READ_RX0     0x0018  // Control Byte read RX buffer
#define CB_READ_CRS     0x0001  // Control byte read Common register using fixed data length

//--------------- Buffer -------------------------------------------
#define MAX_UDP_PACKET_SIZE 1472
uint8_t udpBuffer[MAX_UDP_PACKET_SIZE];

//--------------- RAM-Register -------------------------------------
#define REG_BLINK_ENABLE 128
#define REG_BLINK_DURATION 129
#define REG_RESET_NODE 130
#define REG_SEND_STATUS 131
#define REG_UNCONFIG_NODE 132

//--------------- Hardware-Pins ------------------------------------
#define CONFIG_JUMPER_PIN 35  // needs external pullup - complete config (MAC and node #)
#define WIFI_CONFIG_BUTTON 34 // needs external pullup - starts Wifi Manager in AP mode
#define STATUS_LED_PIN 2

//--------------- Global Variables ---------------------------------
WiFiUDP udp;
uint8_t ethBuffer[1500];
bool useEthernet = false;
bool configMode = false;                                                             // Basic-config (MAC/WiFi)
bool nodeAddrConfig = false;                                                         // Node adress config
bool pwm_toggle = false;
static bool spiInitialized = false;
unsigned long lastBlinkTime = 0;
bool blinkingActive = false;
bool nodeReady = false;
bool netOK = false;
static uint16_t statusCounter = 0;                                                   // Send counter - only used to judge on the host side if packets have been lost.
IPAddress lastSenderIP;
bool nv_changed=false;

//---------- forward declarations ----------------------------------
bool initW5500Raw();
bool initRawUDPSocket();
void updateBlinking();
void saveIPConfigAfterDHCP();
int parseRawUDPPacket();
void processConfigCommand(uint16_t* data, int wordCount);
void processDataCommand(uint16_t* data, int wordCount);
void SendStatus();
void sendRawUDP(IPAddress destIP, uint16_t destPort, uint8_t* data, uint16_t len);
void sendWiFiUDP(IPAddress destIP, uint16_t destPort, uint8_t* data, uint16_t len);

struct IPConfig {
  uint8_t mac[6];
  IPAddress ip;
  IPAddress gateway;
  IPAddress subnet;
  IPAddress dns;
};

IPConfig ethConfig;

  struct NVConfig {
    uint8_t ethAddr[6];
    uint16_t nodeAddr;
    uint16_t pwmCount;          // Number of PWM ports in this node
    uint16_t pwmStartWord;      // Here starts the PWM data in the stream for this node
    uint16_t pwmStartbit;       // Here we bind the first Servo for this node
    uint16_t binOutCount;       // Number of binary ports in this node
    uint16_t binOutStartWord;   // Here starts the bit data for this node
    uint16_t binOutStartbit;    // Tells the start bit where digital ports start Range: 0-15 - means, digital outputs may be mixed with PWM outputs - PWM first 0->X, then Binary X->15
    uint16_t dummy1;            // ... a few further known register place holders to keep CRC intact in case of changes
    uint16_t dummy2;
    uint16_t dummy3;
    uint16_t dummy4;
    uint16_t dummy5;
    uint16_t dummy6;
    uint16_t checksum;
  };
//---------------- PWM Config --------------------------------------
NVConfig nvConfig;
uint16_t ramRegisters[256];                                                          // PWM-Configuration - RAM-Register
#define MAX_PWM_OUTPUTS 16                                                           //16 Pins
#define PWM_FREQUENCY 50
#define PWM_RESOLUTION 12                                                            // 12 bit =4096 steps
uint8_t pwmPins[MAX_PWM_OUTPUTS] = {
  32,33,25,26,27,14,12,13,15,17,0,4,19,21,3,22                                       // Ports in order according to the wiring of the PCB
};
//==================================================================
// Setup after boot
//==================================================================
void setup() {
  Serial.begin(115200);
  pinMode(W5500_RST, OUTPUT);
  pinMode(W5500_SCK, OUTPUT);
  pinMode(W5500_CS, OUTPUT);
  pinMode(W5500_MISO, INPUT);
  pinMode(W5500_MOSI, OUTPUT);
  pinMode(STATUS_LED_PIN, OUTPUT);
  initEEPROM();
    Serial.println(FIRMWARE);
    Serial.print("Ethernet Address in NV: ");
  for (int i=0;i < 6;i++){
    Serial.print(nvConfig.ethAddr[i],HEX);                                           // show ethernet address in NV memory
    Serial.print(" ");
  }
  Serial.println();
  Serial.print("Node Adress: ");
  Serial.println(nvConfig.nodeAddr);
  initNetwork();                                                                     // in case of ethernet only use it to get an address via DHCP    
  if (useEthernet) {                                                                 //set up for the raw W5500 communication
    saveIPConfigAfterDHCP();                                                         // save IP settings for use with W5500 raw communication
    if (initW5500Raw() && initRawUDPSocket()){ 
      useEthernet=true;
      applyIPConfigToW5500();
    } else {
      useEthernet=false;
    }
  }
  if (WiFi.status() == WL_CONNECTED || useEthernet ) {netOK=true;} 
  initPullDowns();                                                                   // for PWM pins
  Serial.println("Start ESP32 PWM-Node");
  initPWM();
  Serial.print("configuration mode: ");
  Serial.println(configMode ? "ACTIVE" : "INACTIVE");
  if (nvConfig.nodeAddr > 0 && netOK==true) {
    Serial.print("Turn on the LED - Node address is set to: ");
    Serial.println(nvConfig.nodeAddr);
    digitalWrite(STATUS_LED_PIN, HIGH);                                              // Show that node has a node address
    nodeReady=true;
  } 
  if (!nodeReady) {
    Serial.println("Node is !!!!! NOT !!!!! ready for operation ");
    Serial.print("Network ready status is: ");
    Serial.println(netOK);
  }
}
//==================================================================
// our main loop
//==================================================================
void loop() {
    if (useEthernet) {
      maintainSocket();  // frequently do mainenance
    } else { 
      maintainWiFiSocket();
    }
    processUDPPackets();
    updateBlinking();
    delay (5);                                                                       // keep the CPU cool
}
//==================================================================
// Mini keepalive to prevent of socket timeouts
//==================================================================
void maintainSocket() {
    static unsigned long lastMaintain = 0;
    if (millis() - lastMaintain < 60000) return;
    
    // Mini-Ping to ourself (127.0.0.1)
    uint8_t ping[] = {0x00};
    sendRawUDP(IPAddress(127,0,0,1), UDP_PORT, ping, 1);
    uint8_t sr = readW5500(S0_SR, 0x08);
    if (sr != 0x22) {  // Nicht im UDP-Modus
        Serial.print("Socket inactive - reinit. Status: 0x");
        Serial.println(sr, HEX);
        // carefully close and re-open
        writeW5500(S0_CR, CB_WRITE_SR0, 0x10);  // CLOSE
        delay(5);
        initRawUDPSocket();
    }
    lastMaintain = millis();
}
//------------------------------------------------------------------
void maintainWiFiSocket() {
    static unsigned long lastWiFiMaintain = 0;
    if (millis() - lastWiFiMaintain < 60000) return;
    
    // Mini-Ping to Broadcast
    uint8_t ping[] = {0x00};
    udp.beginPacket("255.255.255.255", UDP_PORT);
    udp.write(ping, 1);
    udp.endPacket();
    lastWiFiMaintain = millis();
}
//==================================================================
// EEPROM-Functions
//==================================================================
void initEEPROM() {
  EEPROM.begin(EEPROM_SIZE);
  loadNVConfig();                                                                    // load or set default values
  if (nvConfig.checksum != calculateChecksum()) {                                    // Check if the config is valid
    // set standard values
    Serial.println("NV checksum is invalid!");
    setDefaultConfig();
  }
}
//------------------------------------------------------------------
// Load the NV memory into struct 
//------------------------------------------------------------------
void loadNVConfig() {
  EEPROM.get(NV_CONFIG_START, nvConfig);
}
//------------------------------------------------------------------
// Save the NV memory to Chip after a change
//------------------------------------------------------------------
void saveNVConfig() {
  nvConfig.checksum = calculateChecksum();
  EEPROM.put(NV_CONFIG_START, nvConfig);
  EEPROM.commit();
}
//------------------------------------------------------------------
// calc the NV memory checksum
//------------------------------------------------------------------
uint16_t calculateChecksum() {
  uint16_t sum = 0;
  uint16_t* words = (uint16_t*)&nvConfig;
  int numWords = (sizeof(nvConfig) / sizeof(uint16_t)) - 1; // Ohne checksum
  
  for (int i = 0; i < numWords; i++) {
    sum += words[i];
  }
  return sum;
}
//------------------------------------------------------------------
// Init the eeprom to default
//------------------------------------------------------------------
void setDefaultConfig() {
  memset(nvConfig.ethAddr, 0, 6);                                                    // leave MAC completely empty -> 0x00,0x00,0x00,0x00,0x00,0x00
  nvConfig.nodeAddr = 0;
  nvConfig.pwmCount = 0;
  nvConfig.pwmStartWord = 0;
  nvConfig.pwmStartbit = 0;
  nvConfig.binOutCount = 0;
  nvConfig.binOutStartWord = 0;
  nvConfig.binOutStartbit = 0;
  saveNVConfig();                                                                    // ... other default values
  Serial.println("NV Configuration - set all values to default");
}
//==================================================================
// Stop execution - Wait for a reset
//==================================================================
void stopExec() {
  while (1) { delay (1000); }                                                        // stay here and wait for a reset
}
//==================================================================
// Network-Init
//==================================================================
void initNetwork() {
  pinMode(CONFIG_JUMPER_PIN, INPUT);
  pinMode(WIFI_CONFIG_BUTTON, INPUT);
  configMode = (digitalRead(CONFIG_JUMPER_PIN) == LOW);
  bool wifiConfigMode = (digitalRead(WIFI_CONFIG_BUTTON) == LOW);
  checkEthernet();
  if (useEthernet) {                                                                 // Ethernet has Priority when available - means does not start wifi
    initEthernet(configMode);
  } else {                                                                           // No Ethernet -> WiFi  
    if (wifiConfigMode) {
      startWiFiConfigMode();                                                         // start the configuration mode and stay there until the wifi config jumper is removed
    } else {                                                                         // initMAC(configMode);
      connectToWiFi();                                                               // Normal operation using saved WiFi credentials
    }
  }
}
//------------------------------------------------------------------
// check, if a W5500 is connected to the ESP
//------------------------------------------------------------------
void checkEthernet() {                                                               //Tells if the unit has a Ethernet W5500 Module
  digitalWrite(W5500_RST, LOW);                                                      // Hardware Reset
  delay(100);
  digitalWrite(W5500_RST, HIGH);
  delay(1000);
  SPIe.begin(W5500_SCK, W5500_MISO, W5500_MOSI, W5500_CS);                           // SPI Initialisieren
  digitalWrite(W5500_CS, HIGH);                                                      // CS inaktiv
  SPIe.beginTransaction(SPISettings(1000000, MSBFIRST, SPI_MODE0));
  digitalWrite(W5500_CS, LOW);                                                       // read W5500 version register ( Register 039 )
  SPIe.transfer(0x00);                                                               // Read command + Adress-High (nur 0x0F für High-Byte)
  SPIe.transfer(0x39);                                                               // Adress-Low
  SPIe.transfer(0x01);           
  byte version = SPIe.transfer(0x00);
  digitalWrite(W5500_CS, HIGH);
  SPIe.endTransaction();
  SPIe.end();
  if (version == 0x04) {
    Serial.println("W5500 hardware found - Version: 0x04");
    useEthernet = true;
  } else {
    Serial.println("W5500 hardware not found - use WiFi");
    useEthernet = false;
  }
}
//------------------------------------------------------------------
// check for existing MAC and use default MAC in basic config mode
//------------------------------------------------------------------
bool initMAC(bool configMode) {
  if (configMode) {                                                                  // choose MAC
    if (!hasStoredMAC()) {
      byte fixedMac[6] = {0xDE, 0xAD, 0xBE, 0xEF, 0x00, 0x01};                       // Config-Mode and no saved MAC -> use temporary default MAC
      memcpy(mac, fixedMac, 6);
      Serial.print("Use temporary default MAC during configuration: ");
      for(int i=0; i<6; i++) {
        Serial.print(mac[i], HEX); 
        if(i < 5) Serial.print(":");
      }
      Serial.println();
    }
  } else {
    if (hasStoredMAC()){                                                             // if a stored MAC exists use this in any case
      memcpy(mac, nvConfig.ethAddr, 6);
      Serial.print("use saved MAC: ");
    } else {
      byte noMac[6] = {0x00, 0x00, 0x00, 0x00, 0x00, 0x00};
      memcpy(mac, noMac, 6);
      Serial.println("No saved MAC Address - please set jumper and MAC: ");
      return 0;
    }
    Serial.print("MAC: ");                                                           // Print MAC on serial monitor
    for(int i=0; i<6; i++) {
      Serial.print(mac[i], HEX); 
      if(i < 5) Serial.print(":");
    }
    Serial.println();
  }  
  return 1;
}
//------------------------------------------------------------------
// Init the W5500 ethernet Module
//------------------------------------------------------------------
void initEthernet(bool configMode) {
  if (! initMAC(configMode)) {
    useEthernet=false;
    return;                                                                          // MAC setting failed
  }
  digitalWrite(W5500_RST, LOW);
  delay(100);
  digitalWrite(W5500_RST, HIGH);
  delay(1000);
  Serial.println("Start DHCP...");                                                   // Run DHCP 
  if (Ethernet.begin(mac) == 0) {
    Serial.println("init: DHCP failed - got no IP");
    useEthernet = false; 
    return; 
  }
  delay(2000);                                                                       // Wait a moment and check IP
  IPAddress ip = Ethernet.localIP();
  Serial.print("got IP Address: ");
  Serial.println(ip);
  if (ip == INADDR_NONE || ip[0] == 0 || ip[0] == 96) {                              // Check for a valid IP
    Serial.println("initEthernet: got invalid IP");
    useEthernet = false;
    return;
  }
  Serial.println("Ethernet successfully initialized!");
  WiFi.mode(WIFI_OFF);
  useEthernet = true;
  return;
}
//------------------------------------------------------------------
// Ckecks if a stored MAC exists
//------------------------------------------------------------------
bool hasStoredMAC() {                                                                // Checks if a valid IP is saved (not 00:00:00:00:00:00)
  for(int i = 0; i < 6; i++) {
    if(nvConfig.ethAddr[i] != 0x00) return true;
  }
  Serial.println("Oops - seems that we have no stored Ethernet in NV memory");
  return false;
}
//==============================================================================
// Wifi handling
//==============================================================================
void startWiFiConfigMode() {
  Serial.println("Start WiFi Configuration-Mode ...");
  digitalWrite(STATUS_LED_PIN, HIGH);
  WiFiManager wm;
  wm.setConfigPortalTimeout(180);                                                    // 3 Minutes Timeout
  if (!wm.startConfigPortal("ESP32_PWM_Node")) {
    Serial.println("Config Portal failed - restarting");
    ESP.restart();
  }
  Serial.println("WiFi configured and connected!");
  digitalWrite(STATUS_LED_PIN, LOW);
}
//------------------------------------------------------------------
// Connect using stored wifi setup
//------------------------------------------------------------------
void connectToWiFi() {
  WiFi.mode(WIFI_STA);  
  Serial.print("Connect with saved WiFi...");                                        // connect with stored Credentials
  WiFi.begin();
  for (int i = 0; i < 30 && WiFi.status() != WL_CONNECTED; i++) {
    delay(500);
    Serial.print(".");
  }
  if (WiFi.status() == WL_CONNECTED) {
    Serial.println("\nWiFi connected!");
    Serial.print("IP: ");
    Serial.println(WiFi.localIP());
    Serial.print("RSSI: ");
    Serial.println(WiFi.RSSI());
    startWiFiUDP();
  } else {
    Serial.println("\nWiFi connection failed");                                      // Kein automatischer Fallback!
  }
}
void startWiFiUDP() {
  if (udp.begin(UDP_PORT)) {
    Serial.print("WiFi UDP started on port ");
    Serial.println(UDP_PORT);
    udp.beginPacket("255.255.255.255", UDP_PORT);                                    // allow to receive Broadcasts
    udp.endPacket();
  } else {
    Serial.println("WiFi UDP start failed");
  }
}
//------------------------------------------------------------------
// Send via wifi UDP 
//------------------------------------------------------------------
void sendWiFiUDP(IPAddress destIP, uint16_t destPort, uint8_t* data, uint16_t len) {
  udp.beginPacket(destIP, destPort);
  udp.write(data, len);
  Serial.print("Sent a data packet via Wifi to Port:/IP: ");
  Serial.print(destPort);
  Serial.print(" ");
  Serial.println(destIP);
  udp.endPacket();
}
//==================================================================
// PWM-Initializing and port init
//==================================================================
void initPWM() {
  for (int i = nvConfig.pwmStartbit; i < (nvConfig.pwmCount+nvConfig.pwmStartbit) && i < MAX_PWM_OUTPUTS; i++) {
    analogWriteFrequency(pwmPins[i],PWM_FREQUENCY);                                  // 50Hz for Servos
    analogWriteResolution(pwmPins[i],PWM_RESOLUTION);
    pinMode(pwmPins[i], OUTPUT);
    analogWrite(pwmPins[i], 0);
  }
}
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

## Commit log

2026-02-08 Update esp32_pwm1.2.ino - adding license
2026-02-09 Add a data flowhart
    This data flowchart shows the datagram structure of a broadcast packets sent to the network

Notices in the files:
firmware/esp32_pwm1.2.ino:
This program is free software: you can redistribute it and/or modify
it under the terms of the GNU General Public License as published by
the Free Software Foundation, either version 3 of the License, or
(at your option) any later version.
